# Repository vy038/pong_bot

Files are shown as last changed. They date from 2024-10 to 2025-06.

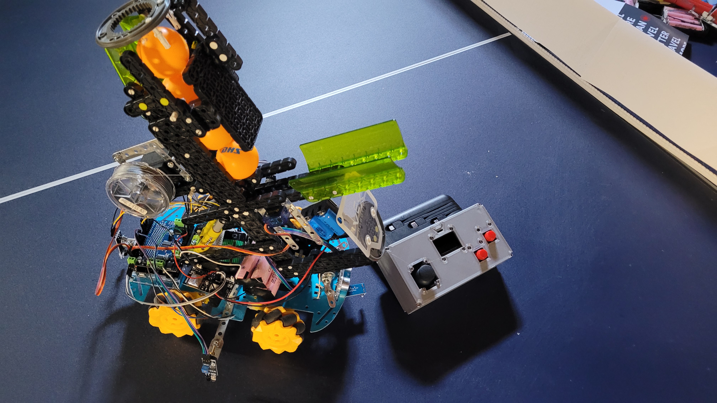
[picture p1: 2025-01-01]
20241005_104122.jpg

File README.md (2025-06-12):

# PONG BOT V 1.5



Manual Control Demo <br>
Pong_BotManualDemo-ezgif com-optimize

Auto Control Demo <br>
Pong_BotAutoDemo-ezgif com-optimize

An advanced and ambitious project I wanted to make with some spare parts and kits in my home, where a robot would be placed on a ping pong table with a bunch of ping pong balls inside. A gun with a firing mechanism I designed would lay on top of a chassis with omnidirectional wheels and IR distance sensors on the back and sides. The robot would be completely autonomous, using a random number generator to decide where to move (uses sensors to ensure it doesn’t fall off the table), and when to fire a ball. The gun was designed to hold multiple balls, allowing me to practice playing ping pong alone. It also has an ESP32 devkit attached to wirelessly receive signals from a wireless controller, allowing it to switch from manual to autonomous. I will soon change this project from being loop-driven to being interrupt-driven to make it more efficient and clean up the code.

# CHANGE LOG
V1:
There would be a DC motor (although I could not find a strong one, I will get that later for an upgrade), that would pull on a string attached to a firing pin, and once it pulls back a certain amount, the pin would lock into place and a ping pong ball will fall in front of it. There will be a servo just underneath where the pin locks in, and it would push down on it, unlocking the pin (which has powerful springs), and forcefully hitting the ball, making it fly out of the gun, and also locking the next ball in queue on top of the pin, so the process can repeat with the next ball. I had to learn a lot of new concepts to try and make this work, including having to use millis() instead of delay() so it would not interrupt anything, and also learned how to design mechanisms that would prove effective and learned about supersizing a lot of my projects, as this was by far one of my biggest, requiring a total of 5 DC motors (controlled with a motor shield consisting of 2 L293Ds, and the last motor being controlled by an external L293D), a servo, and 3 IR proximity sensors. 

Some improvements that can currently be made include some improvements to the power supply, as the power currently being supplied to the bot is nowhere near enough to power the motors, and also getting a stronger motor/different mechanism to pull the pin, as a DC gear motor is not strong enough (use servo motor). This will be improved upon in the second version. 

UPDATE 1.2 (2024-04-13):
The firing mechanism now works perfectly, due to the swapping out of a weak DC hobby motor for a continuous servo, and moving the location from the front of the gun to the back, because I noticed throughout a lot of my trials, whenever I went to cock the pin back, I always did it from the top because it was much easier instead of where the motor was pulling, so moving it helped alleviate a lot of the stress on the motor and allowed it to fully pull the pin back. I also created a 3D design of a pulley/wheel attachment for the servo and got it 3D printed to be used for the servo. However, the printer was not precise enough to print out the teeth of the wheel to mount on the servo, so I had to super glue an existing servo head on top to create a reliable mount. Also, removing the DC motor helps bring the power requirement down a lot, and it now doesn’t require the extra L293D chip that I had originally.

Minor Update (2024-04-14):
Added 3 18650 Li-ion batteries to try and power it up, putting two in parallel and one in series to another, but the motors would still not run. I also added an extension to the ball holder so now it can hold up to 4 balls. I plan on taking a break / doing more research into why the motors are not working (could still be that there is not enough current). Motors work fine independently, but when run with other motors at the same time, only one of them runs. The current of 1 motor measured without load is ~200mA, and with load ~550mA.

Minor Update (2024-04-15):
Managed to get the motor movement working at the same time as the servo firing mechanism, the only thing left to do is change the motor speed for each one (some are faster than others, which can easily be done with trial and error), get the IR distance sensors working, tune some values for servo firing mech (optional), and add more batteries to the battery pack (optional). Turns out the problem was not the power supply, but an issue with my code. The IR distance sensors were later fixed so it could successfully detect edges and move the bot accordingly, however, the bot's movement is rather erratic, and it keeps moving in a circle, probably due to some motors not getting enough power, which could be a motor problem or the battery is not big enough. I will try to expand the battery size later and add heatsinks for the chips after.

Minor Update (2024-04-18):
Added one more battery in parallel to the lone battery as an attempt to get the current up, still to no avail. After some more experimentation and further research, the problem seems to be the motor driver (driver bought from China, but based on the Adafruit Motor Shield V1), which many people online say is a “worthless piece of junk” and should be “chucked as far as possible.” This is mainly because the chips (L293Ds) are considered ancient, and even Adafruit discontinued it in exchange for the Adafruit Motor Shield V2, so, if possible, I will try and research a better alternative to the current moro shield, one that is hopefully able to distribute current more evenly amongst motors. Although it could just be bad quality on the manufacturer’s part, as I got it for ~$1 from China, so I will try to test with a higher quality shield too.

Minor Update (2024-05-25):
Got a new motor driver shield (same model), but there was no difference when I swapped them out, the same issue was still present, which could mean two things: the model of the motor driver is bad, or it is the fault of the motors (unlikely, because I tested the motors and they seemed fine). Also attached a gyroscope to the robot, and made it adjust for the minor turns, but that didn’t end up working either, might polish up the gyroscope code later. Can also try to use another motor driver I have at home that can only give commands to two motors, but can make it work if the wheels are given commands in an ‘X’ shape, still allowing it to move all 4 directions but only controlling two motors at a time.

Update (2024-08-22):
Replaced the motor driver shield again, but this time for the Adafruit motor driver shield V2, which is way more energy efficient. This also shows in the final result, as the differences in motor voltage dropped drastically, and really only shows when the bot has to travel long distances, which it won’t have to do anyways. The real problem with the motors moving inconsistently however, was the uneven weight distribution, as a lot of the heavy batteries were at the back of the car, so moving them to the front solved the issue. However, another problem arose where the servo that pulls the trigger back is not strong enough. I then replaced the SG90 with a stronger MG995, and also cut the trace on the motor shield V2 to connect an ext. Power supply to the MG995. I had to also solder and make a modification to the shield which allowed for the other servo to remain on regulated 5V power if needed. The only things left to do now are to 3D print a bigger wheel for the MG995 to pull the trigger (3D model done, waiting on print), and also to wait for a four AA battery holder to supply 6V external power to the servo(s) with good current. Once that is done and no further problems arise, the project will be finished.

Change (2024-08-27):
Not really a change, but added a different mode to the robot. Attached an ESP32 to the robot to communicate with the Arduino for wireless control. Hooked up the circuit from ESP games (ESP galga circuitry) and turned it into a controller for the robot, controlling where it moves and shoots. Aside from that, no major changes besides adding a US sensor to the front for net avoidance.

Big Update (2024-09-08):
UPDATE 1.5: Added dual modes for the robot, allowing it to switch from auto to manual. Also managed to find a $1 fishing line reel that is the right size for the MG995 motor, and was able to successfully pull back the firing pin with no effort. I also added a new support to the motor, securing it more soundly to the top edge of the gun, preventing a lot of the bending of the gun as the trigger is pulled. I also switched a lot of the power supplies around; hooked the two li-ion batteries to a 5V regulator on the breadboard (had to also rewire some of the stuff on there), using it to directly power the sensors and common grounding it with the Arduino. Using regulated li-ion batteries ensured that the servos had enough current they needed, but also didn’t get overloaded with voltage, operating at a steady 5V. I then used a simple 9V battery to power just the Arduino for the logic, utilizing the Vin pin.

Small Changes (2024-10-01)
Added an edge sensor to the front of the bot in case it decides to turn around and run over the edge of the table (it did that and broke before), and if possible, secure gun more firmly to chassis to prevent it from wiggling as bot moves around. Aside from that, I 3D printed a cover for the game console that improves the look and appeal of the bot to others.

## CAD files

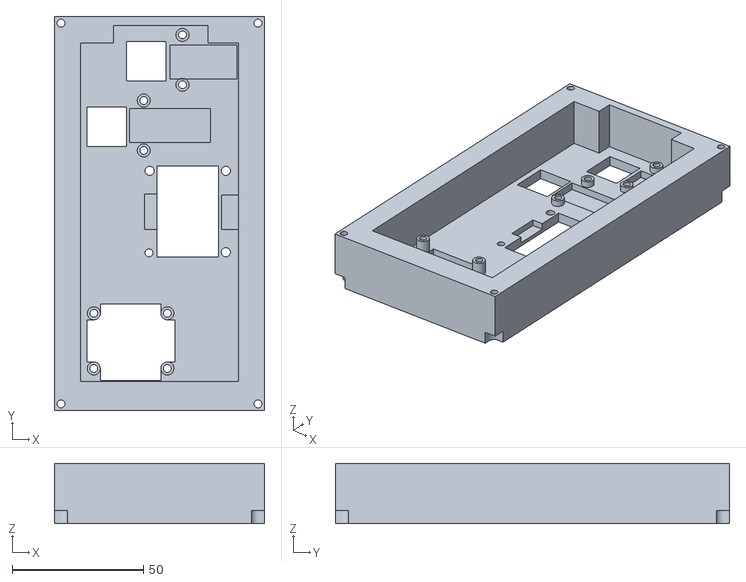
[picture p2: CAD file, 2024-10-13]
pong_bot/pong_bot_V1.5_files/esp32_controller_V1.2/(UPDATED) Game Console Top Shell.stl
80.0 x 150.0 x 23.0

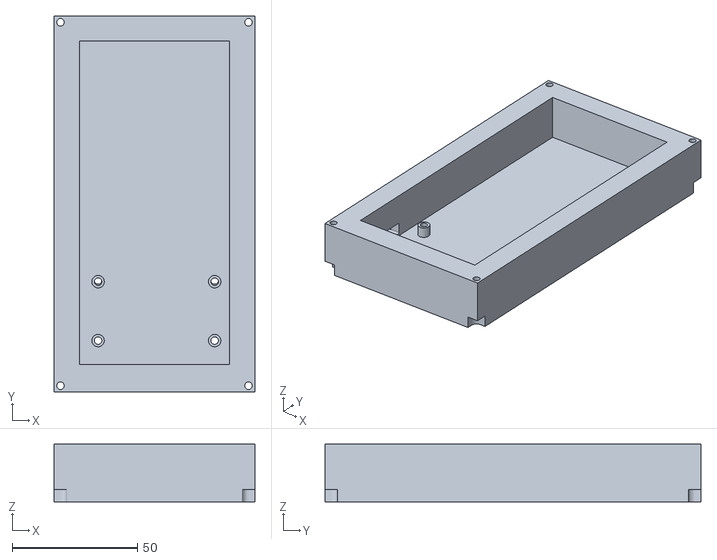
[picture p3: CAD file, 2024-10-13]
pong_bot/pong_bot_V1.5_files/esp32_controller_V1.2/Game Console Bottom Shell.stl
80.0 x 150.0 x 23.0

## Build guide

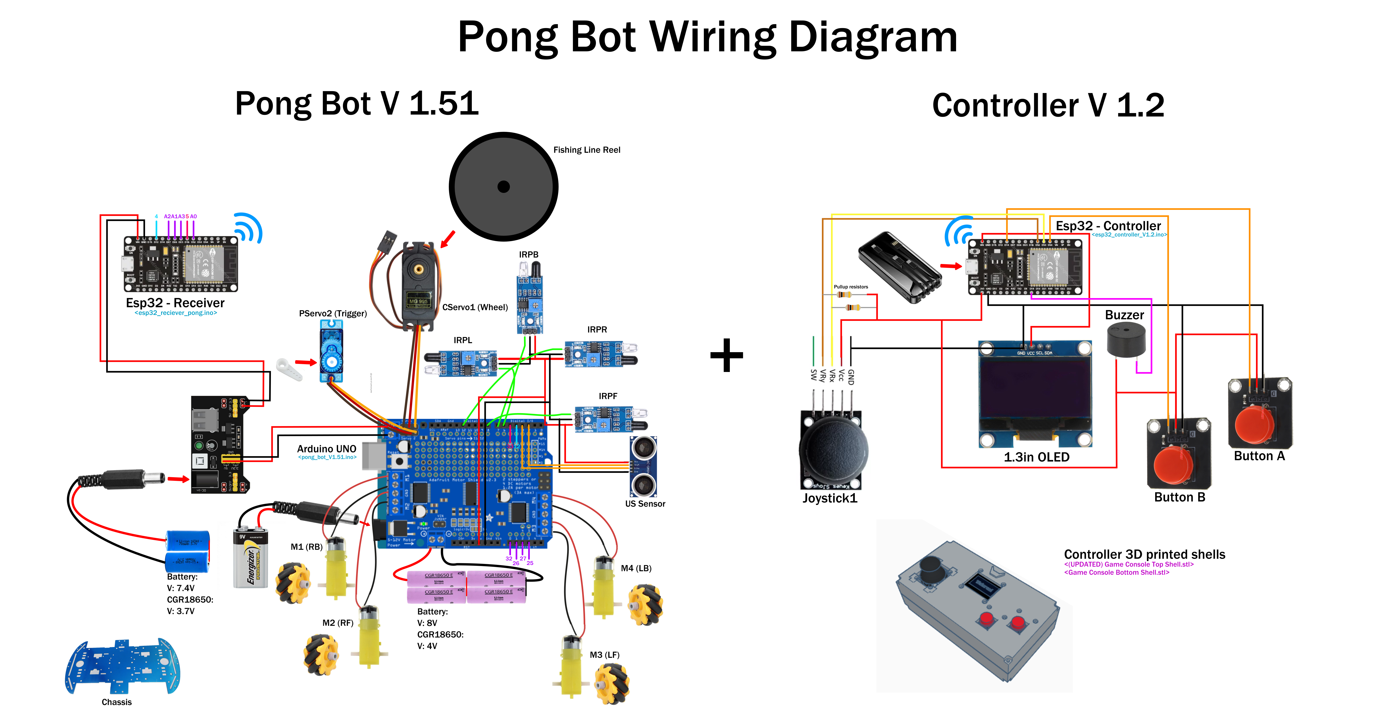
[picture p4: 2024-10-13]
pong_bot/pong_bot_V1.5_files/Wiring Diagram (pong_bot).png

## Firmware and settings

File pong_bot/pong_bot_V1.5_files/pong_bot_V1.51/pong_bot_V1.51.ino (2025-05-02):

/*
Ping Pong Bot
Version 1.51
Victor Yu
Created: 2024-04-06
Modified: 2024-09-15

Purpose:
This is a robot that is intended to move around one side of a ping pong table 
(with distance sensors so it doesn't fall off), and fire ping pong balls at the user for training
This has two modes, auto and manual. The robot moves and fires autonomously in auto, and manual has everything being controlled by a controller.
*/

// libraries
#include <Adafruit_MotorShield.h>
#include <Servo.h>

// i2c address for shield
Adafruit_MotorShield AFMS = Adafruit_MotorShield();

// DC motors definition
Adafruit_DCMotor *motorRB = AFMS.getMotor(1);
Adafruit_DCMotor *motorRF = AFMS.getMotor(2);
Adafruit_DCMotor *motorLF = AFMS.getMotor(3);
Adafruit_DCMotor *motorLB = AFMS.getMotor(4);

// define servos
Servo servoPull;
Servo servoWheel;

// pin definitions of sensors
const int leftIRSensor = 6;
const int backIRSensor = 7;
const int rightIRSensor = 12;
const int frontIRSensor = 8;

// define where us sensor is
const int TRIG_PIN = 2;
const int ECHO_PIN = 3;
float duration;
long frontDistance;

// controller variables
const int buttonA = 4;
const int buttonB = 5;
const uint8_t backward = A2;
const uint8_t forward = A1;
const uint8_t left = A0;
const uint8_t right = A3;

// logic variables for the robot to decide when to fire
int decision = 0;
int fireOrNo = 1;
int armed = 0;

// timer stuff for firing
unsigned long startMillisFiring; 
unsigned long currentMillisFiring;

// general timer stuff
unsigned long startMillis;
unsigned long currentMillis;

// robot mode (manual / auto)
int mode = 0;

void setup() {
  // serial monitor
  Serial.begin(9600);

  // connect to motor driver shield
  if (!AFMS.begin()) {  // create with the default frequency 1.6KHz
                        // if (!AFMS.begin(1000)) {  // OR with a different frequency, say 1KHz
    Serial.println("Could not find Motor Shield. Check wiring.");
    while (1);
  }
  Serial.println("Motor Shield found.");

  // configure sensor pin modes
  pinMode(leftIRSensor, INPUT);
  pinMode(backIRSensor, INPUT);
  pinMode(rightIRSensor, INPUT);
  pinMode(frontIRSensor, INPUT);

  // configure pins for distance sensor
  pinMode(TRIG_PIN, OUTPUT);
  pinMode(ECHO_PIN, INPUT);

  // input pins for controller
  pinMode(buttonA, INPUT);
  pinMode(buttonB, INPUT);
  pinMode(forward, INPUT);
  pinMode(backward, INPUT);
  pinMode(left, INPUT);
  pinMode(right, INPUT);

  // set up the trigger servo
  servoPull.attach(9);
  servoPull.write(180);

  // configure wheel servo
  servoWheel.attach(10);

  // configure motors
  motorRB->setSpeed(140);
  motorRF->setSpeed(140);
  motorLF->setSpeed(140);
  motorLB->setSpeed(140);

  motorRB->run(RELEASE);
  motorRF->run(RELEASE);
  motorLF->run(RELEASE);
  motorLB->run(RELEASE);

  // set random seed for robot decision making
  randomSeed(analogRead(0));

  // arm the robot (pull firing pin back)
  if (armed == 0) {
    servoPull.write(180);
    delay(500);
    servoWheel.write(130);
    delay(950);
    servoWheel.write(0);
    delay(400);
    armed = 1;
  }

  // redeclare values of variables for when mode changes
  decision = 0;
  fireOrNo = 1;
  currentMillisFiring = 0;
  currentMillis = 0;

  // start general timers
  startMillisFiring = millis();
  startMillis = millis();

  while (true) {
    if (mode == 0) {        // MANUAL MODE
      if (IRRead() == 0) {  // if all sensors detect that the bot is not on an edge or near a wall
        // code for controlled movement and firing here

        if ((digitalRead(right) == 1 || digitalRead(left) == 1) && digitalRead(backward) == LOW && digitalRead(forward) == LOW) {  // movement for true side
          side(digitalRead(right), digitalRead(buttonB));
        } else if ((digitalRead(backward) == 1 || digitalRead(forward) == 1) && digitalRead(right) == LOW && digitalRead(left) == LOW) {  // movement for true forward/backward
          forwardFunc(digitalRead(forward));
        } else if ((digitalRead(backward) == 1 || digitalRead(forward) == 1) && (digitalRead(right) == 1 || digitalRead(left) == 1)) {  // movement for diagonals/turns
          if (digitalRead(buttonB) == HIGH) {               // turn or
            side(digitalRead(right), digitalRead(buttonB));
          } else {                                          // go diagonal
            diagonal(digitalRead(forward), digitalRead(left));
          }
        } else {  // stop the bot
          motorRB->run(RELEASE);
          motorRF->run(RELEASE);
          motorLF->run(RELEASE);
          motorLB->run(RELEASE);
        }

        if (digitalRead(buttonA) == HIGH && digitalRead(buttonB) == HIGH) {  // change modes and reset all timers once both buttons are pressed at the same time
          motorRB->run(RELEASE);
          motorRF->run(RELEASE);
          motorLF->run(RELEASE);
          motorLB->run(RELEASE);
          delay(750);
          mode = 1;
          break;

        } else if (digitalRead(buttonA) == HIGH) {  // fire when 'a' button is pressed
          fire();
        }


      } else {  // if bot is on the edge of table, move away

        Serial.println("Edge readings");
        Serial.print(digitalRead(frontIRSensor));
        Serial.print(" ");
        Serial.print(digitalRead(backIRSensor));
        Serial.print(" ");
        Serial.print(digitalRead(leftIRSensor));
        Serial.print(" ");
        Serial.println(digitalRead(rightIRSensor));

        // takes cases form the IRRead() function and moves the bot accordingly (moves away from edge or wall)
        if (IRRead() == 1) {
          side(0, 0);
          delay(500);
        } else if (IRRead() == 2) {
          side(1, 0);
          delay(500);
        } else if (IRRead() == 3) {
          forwardFunc(1);
          delay(500);
        } else {
          forwardFunc(0);
          delay(500);
        }
      }

      delay(10);

    } else {                // AUTO MODE
      if (IRRead() == 0) {  // if all sensors detect that the bot is not on an edge or near a wall
        // code for random movement and firing here

        currentMillis = millis();                                 // get the current "time" (actually the number of milliseconds since the program started)
        if (currentMillis - startMillis >= random(2000, 4000))  { // test whether the period has elapsed, adjust milisecond delay (2000 - 4000) as needed                                                 
          // random movement decision
          decision = random(1, 5);
          if (fireOrNo != -1) {  // seperate random variable to see if the robot should fire a ball or not
            fireOrNo = random(1, 9);
          }
          Serial.println(fireOrNo);
          startMillis = currentMillis;  // IMPORTANT to save the start time of the current time
        }

        // uses the random number generated at a random time to determine which direction to move in
        if (decision == 1) {
          forwardFunc(1);
          Serial.println("fwd");
        } else if (decision == 2) {
          forwardFunc(0);
          Serial.println("bck");
        } else if (decision == 3) {
          side(1, 0);
          Serial.println("left");
        } else if (decision == 4) {
          side(0, 0);
          Serial.println("right");
        }

        // uses a random number generated periodically to see whether the bot should stop and fire a ball randomly
        if (fireOrNo >= 7) {
          fireOrNo = -1;
          Serial.println("FIRE");
          motorRB->run(RELEASE);
          motorRF->run(RELEASE);
          motorLF->run(RELEASE);
          motorLB->run(RELEASE);
          fire();
        }

        if (digitalRead(buttonA) == HIGH && digitalRead(buttonB) == HIGH) {  // change modes and reset all timers
          motorRB->run(RELEASE);
          motorRF->run(RELEASE);
          motorLF->run(RELEASE);
          motorLB->run(RELEASE);
          delay(750);
          mode = 0;
          break;
        }


      } else {  // if bot is on the edge of table, move away
        Serial.println("Edge readings");
        Serial.print(digitalRead(frontIRSensor));
        Serial.print(" ");
        Serial.print(digitalRead(backIRSensor));
        Serial.print(" ");
        Serial.print(digitalRead(leftIRSensor));
        Serial.print(" ");
        Serial.println(digitalRead(rightIRSensor));

        // takes cases form the IRRead() function and moves the bot accordingly (moves away from edge or wall)
        if (IRRead() == 1) {
          side(0, 0);
          decision = 4;
          delay(random(500, 1000));
        } else if (IRRead() == 2) {
          side(1, 0);
          decision = 3;
          delay(random(500, 1000));
        } else if (IRRead() == 3) {
          forwardFunc(1);
          decision = 1;
          delay(random(500, 1000));
        } else {
          decision = 2;
          forwardFunc(0);
          delay(random(500, 1000));
        }
      }

      delay(10);
    }
  }
}

void loop() { // used when loop is broken out of, returns back to setup to restart everything (ususally used when changing modes)
  setup();
}

// move forward function (or backwards, depending on input variable)
void forwardFunc(int dir) {
  switch (dir) {
    case 0:  // backwards
      motorRB->run(BACKWARD);
      motorRF->run(BACKWARD);
      motorLF->run(BACKWARD);
      motorLB->run(BACKWARD);
      break;
    case 1:  // forwards
      motorRB->run(FORWARD);
      motorRF->run(FORWARD);
      motorLF->run(FORWARD);
      motorLB->run(FORWARD);
      break;
  }
}

// move left or right depending in input variable (0 is right, 1 is left)
void side(int dir, int buttonState) {
  if (buttonState == 1) {
    switch (dir) {
      case 0:  // to the right
        motorRB->run(BACKWARD);
        motorRF->run(BACKWARD);
        motorLF->run(FORWARD);
        motorLB->run(FORWARD);
        break;
      case 1:  // to the left
        motorRB->run(FORWARD);
        motorRF->run(FORWARD);
        motorLF->run(BACKWARD);
        motorLB->run(BACKWARD);
        break;
    }
  } else {
    switch (dir) {
      case 0:  // to the right
        motorRB->run(BACKWARD);
        motorRF->run(FORWARD);
        motorLF->run(BACKWARD);
        motorLB->run(FORWARD);
        break;
      case 1:  // to the left
        motorRB->run(FORWARD);
        motorRF->run(BACKWARD);
        motorLF->run(FORWARD);
        motorLB->run(BACKWARD);
        break;
    }
  }
}

// move the bot in diagonal directions, using only two inputs
void diagonal(int F, int L) {
  if (F == 1) {  // either FL or FR
    switch (L) {
      case 0:  // to the right (FR)
        motorRB->run(FORWARD);
        motorRF->run(RELEASE);
        motorLF->run(FORWARD);
        motorLB->run(RELEASE);
        break;
      case 1:  // to the left (FL)
        motorRB->run(RELEASE);
        motorRF->run(FORWARD);
        motorLF->run(RELEASE);
        motorLB->run(FORWARD);
        break;
    }
  } else {  // either BL or BR
    switch (L) {
      case 0:  // to the right (BR)
        motorRB->run(RELEASE);
        motorRF->run(BACKWARD);
        motorLF->run(RELEASE);
        motorLB->run(BACKWARD);
        break;
      case 1:  // to the left (BL)
        motorRB->run(BACKWARD);
        motorRF->run(RELEASE);
        motorLF->run(BACKWARD);
        motorLB->run(RELEASE);
        break;
    }
  }
}

// firing procedure (CONFIGURE ROTATION AMOUNT TO ACCOUNT FOR MG995 WHEEL)
void fire() {  //fires a ball, works fine, adjust timing (Maybe replace with milis()?)

  // stop all motors
  motorRB->run(RELEASE);
  motorRF->run(RELEASE);
  motorLF->run(RELEASE);
  motorLB->run(RELEASE);

  // STAGE 1: pull firing pin, firing ball
  servoPull.write(0);
  Serial.println("STAGE 1");
  delay(500);

  // STAGE 2: turn motor with string back to original position for 750 ms
  Serial.println("STAGE 2");
  servoPull.write(180);
  delay(500);

  Serial.println("STAGE 2.5");
  servoWheel.write(130);
  delay(950);

  // STAGE 3: return motor to og pos
  Serial.println("STAGE 3");
  servoWheel.write(0);
  delay(400);

  // reset stage after 500 ms grace period
  Serial.println("ENDED FIRING");
  fireOrNo = 1;
}

/* reads the sensors on the side and distance sensor at the front
  * returns 0: all is well
  * returns 1: left edge
  * returns 2: right edge
  * returns 3: back edge
  * returns 4: front wall
*/
int IRRead() {
  /************ Start US Measurement Section ***********/
  digitalWrite(TRIG_PIN, LOW);
  delayMicroseconds(2);
  digitalWrite(TRIG_PIN, HIGH);
  delayMicroseconds(10);
  digitalWrite(TRIG_PIN, LOW);
  duration = pulseIn(ECHO_PIN, HIGH);
  frontDistance = duration * 0.034 / 2;
  /************** End US Measurement Section ***********/


  // read the sensor data and return function values
  if (digitalRead(leftIRSensor) == LOW && digitalRead(backIRSensor) == LOW && digitalRead(rightIRSensor) == LOW && digitalRead(frontIRSensor) == LOW && frontDistance > 10) {
    return 0;
  } else if (digitalRead(leftIRSensor) == HIGH) {
    return 1;
  } else if (digitalRead(rightIRSensor) == HIGH) {
    return 2;
  } else if (digitalRead(backIRSensor) == HIGH) {
    return 3;
  } else if (digitalRead(frontIRSensor) == HIGH){
    return 4;
  } else {
    return 5;
  }
}

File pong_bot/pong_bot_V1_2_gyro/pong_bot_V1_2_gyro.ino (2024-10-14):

/*
Ping Pong Bot
Version 1.2
Victor Yu
Created: 2024-04-06
Modified: 2024-04-13

Purpose:
This is a robot that is intended to move around one side of a ping pong table 
(with distance sensors so it doesn't fall off), and fire ping pong balls at the user for training
*/

#include <AFMotor.h>
#include <Servo.h>
#include <Wire.h>

const int MPU = 0x68; // MPU6050 I2C address
float AccX, AccY, AccZ;
float GyroX, GyroY, GyroZ;
float accAngleX, accAngleY, gyroAngleX, gyroAngleY, gyroAngleZ;
float roll, pitch, yaw;
float AccErrorX, AccErrorY, GyroErrorX, GyroErrorY, GyroErrorZ;
float elapsedTime, currentTime, previousTime;
int c = 0;

// DC motors
AF_DCMotor motorRB(1);
AF_DCMotor motorRF(2);
AF_DCMotor motorLF(3);
AF_DCMotor motorLB(4);

Servo servoPull;
Servo servoWheel;

int leftIRSensor = 15;
int backIRSensor = 16;
int rightIRSensor = 17;

unsigned long startMillisFiring;  //some global variables available anywhere in the program
unsigned long currentMillisFiring;

unsigned long startMillis;  //some global variables available anywhere in the program
unsigned long currentMillis;

int decision;
int fireOrNo = 1;


const int inSpeedRB = 100;
const int inSpeedRF = 100;
const int inSpeedLF = 150;
const int inSpeedLB = 150;
int speedRB = inSpeedRB;
int speedRF = inSpeedRF;
int speedLF = inSpeedLF;
int speedLB = inSpeedLB;

void setup() {
  Serial.begin(9600);  // set up Serial library at 9600 bps

  pinMode(leftIRSensor, INPUT);
  pinMode(backIRSensor, INPUT);
  pinMode(rightIRSensor, INPUT);


  servoPull.attach(9);
  servoPull.write(180);

  motorRB.setSpeed(speedRB);
  motorRF.setSpeed(speedRF);
  motorLF.setSpeed(speedLF);
  motorLB.setSpeed(speedLB);
  motorRB.run(RELEASE);
  motorRF.run(RELEASE);
  motorLF.run(RELEASE);
  motorLB.run(RELEASE);

  randomSeed(analogRead(0));

  servoWheel.attach(10);

  Wire.begin();                      // Initialize comunication
  Wire.beginTransmission(MPU);       // Start communication with MPU6050 // MPU=0x68
  Wire.write(0x6B);                  // Talk to the register 6B
  Wire.write(0x00);                  // Make reset - place a 0 into the 6B register
  Wire.endTransmission(true);        //end the transmission
  calculate_IMU_error();
  delay(20);
  
  servoPull.write(180);
  delay(500);
  servoWheel.write(160);
  delay(950);
  servoWheel.write(20);
  delay(400);
  servoWheel.write(90);

  startMillisFiring = millis();
  startMillis = millis();
}

void loop() {
  if (IRRead() == 0) {
    //code for random movement and firing here

    currentMillis = millis();                               //get the current "time" (actually the number of milliseconds since the program started)
    if (currentMillis - startMillis >= random(2000, 4000))  //test whether the period has elapsed, adjust milisecond delay (2000 - 4000) as needed
    {
      decision = random(1, 5);
      if (fireOrNo != -1) {
        fireOrNo = random(1, 9);
        Serial.println("eibwefwewerwewrewreewrwrerewrewrewrewwrewrewrewer");
      }
      Serial.println(fireOrNo);
      startMillis = currentMillis;  //IMPORTANT to save the start time of the current time
    }

    if (decision == 1) {
      //forward(1);
      Serial.println("fwd");

      speedRF = inSpeedRF + pitch*2.5;
      speedLF = inSpeedLF - pitch*2.5;
    } else if (decision == 2) {
      forward(1);
      Serial.println("bck");

      speedRF = inSpeedRF - pitch*2.5;
      speedLF = inSpeedLF + pitch*2.5;
    } else if (decision == 3) {
      side(1);
      Serial.println("left");

      speedRF = inSpeedRF + pitch*2.5;
      speedLF = inSpeedLF + pitch*2.5;
    } else if (decision == 4) {
      side(0);
      Serial.println("right");

      speedRF = inSpeedRF - pitch*2.5;
      speedLF = inSpeedLF - pitch*2.5;
    }

    
    motorRB.setSpeed(speedRB);
    motorRF.setSpeed(speedRF);
    motorLF.setSpeed(speedLF);
    motorLB.setSpeed(speedLB);

    if (fireOrNo >= 7) {
      fireOrNo = -1;
      Serial.println("FIRE!!!!!!!!!!!!!!!!!!!!!!!!!!!!!!!!!!!!!!!!!!!!!!!!!!!!!!!!!!!!!!!!!");
      motorRB.run(RELEASE);
      motorRF.run(RELEASE);
      motorLF.run(RELEASE);
      motorLB.run(RELEASE);
      fire();
    }




  } else {
    Serial.println("Edging");
    Serial.print(digitalRead(A1));
    Serial.print(" ");
    Serial.print(digitalRead(A2));
    Serial.print(" ");
    Serial.println(digitalRead(A3));
    if (IRRead() == 1) {
      side(0);
      delay(random(500, 1500));
    } else if (IRRead() == 2) {
      side(1);
      delay(random(500, 1500));
    } else {
      forward(1);
      delay(random(500, 1500));
    }
  }

  // === Read acceleromter data === //
  Wire.beginTransmission(MPU);
  Wire.write(0x3B); // Start with register 0x3B (ACCEL_XOUT_H)
  Wire.endTransmission(false);
  Wire.requestFrom(MPU, 6, true); // Read 6 registers total, each axis value is stored in 2 registers
  //For a range of +-2g, we need to divide the raw values by 16384, according to the datasheet
  AccX = (Wire.read() << 8 | Wire.read()) / 16384.0; // X-axis value
  AccY = (Wire.read() << 8 | Wire.read()) / 16384.0; // Y-axis value
  AccZ = (Wire.read() << 8 | Wire.read()) / 16384.0; // Z-axis value
  // Calculating Roll and Pitch from the accelerometer data
  accAngleX = (atan(AccY / sqrt(pow(AccX, 2) + pow(AccZ, 2))) * 180 / PI) - 0.58; // AccErrorX ~(0.58) See the calculate_IMU_error()custom function for more details
  accAngleY = (atan(-1 * AccX / sqrt(pow(AccY, 2) + pow(AccZ, 2))) * 180 / PI) + 1.58; // AccErrorY ~(-1.58)
  // === Read gyroscope data === //
  previousTime = currentTime;        // Previous time is stored before the actual time read
  currentTime = millis();            // Current time actual time read
  elapsedTime = (currentTime - previousTime) / 1000; // Divide by 1000 to get seconds
  Wire.beginTransmission(MPU);
  Wire.write(0x43); // Gyro data first register address 0x43
  Wire.endTransmission(false);
  Wire.requestFrom(MPU, 6, true); // Read 4 registers total, each axis value is stored in 2 registers
  GyroX = (Wire.read() << 8 | Wire.read()) / 131.0; // For a 250deg/s range we have to divide first the raw value by 131.0, according to the datasheet
  GyroY = (Wire.read() << 8 | Wire.read()) / 131.0;
  GyroZ = (Wire.read() << 8 | Wire.read()) / 131.0;
  // Correct the outputs with the calculated error values
  GyroX = GyroX + 0.56; // GyroErrorX ~(-0.56)
  GyroY = GyroY - 2; // GyroErrorY ~(2)
  GyroZ = GyroZ + 0.79; // GyroErrorZ ~ (-0.8)
  // Currently the raw values are in degrees per seconds, deg/s, so we need to multiply by sendonds (s) to get the angle in degrees
  gyroAngleX = gyroAngleX + GyroX * elapsedTime; // deg/s * s = deg
  gyroAngleY = gyroAngleY + GyroY * elapsedTime;
  yaw =  yaw + GyroZ * elapsedTime;
  // Complementary filter - combine acceleromter and gyro angle values
  gyroAngleX = 0.96 * gyroAngleX + 0.04 * accAngleX;
  gyroAngleY = 0.96 * gyroAngleY + 0.04 * accAngleY;

  roll = gyroAngleX;
  pitch = gyroAngleY;
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
